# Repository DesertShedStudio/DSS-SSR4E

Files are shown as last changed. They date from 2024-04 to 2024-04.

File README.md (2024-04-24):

DSS-SSR4E
============

The "DSS-SSR4E" is a OSHWA Certified hardware design, providing four isolated SSR outputs and a single isolated
ABZ encoder input. Compatible with Mesa Ethernet Anything I/O Cards and Mesa Electronics HostMot2 configurations.

DSS-SSR4E <br>
"Desert Shed Stuido SSR x4 + Encoder"



This repository is aimed towards those who wish to manufacture their own boards. 

Media
=======

| KICAD RENDER | HAND SOLDERED PROTOTYPE  |
| --- | --- |
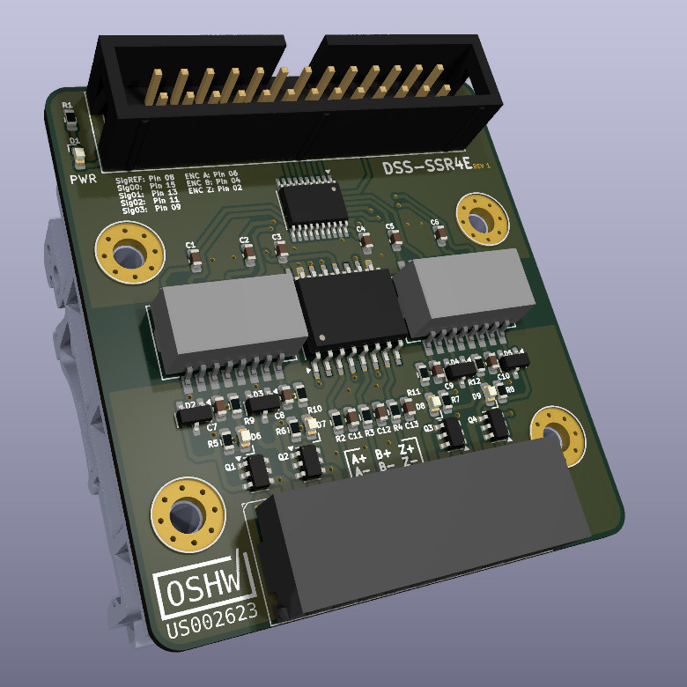
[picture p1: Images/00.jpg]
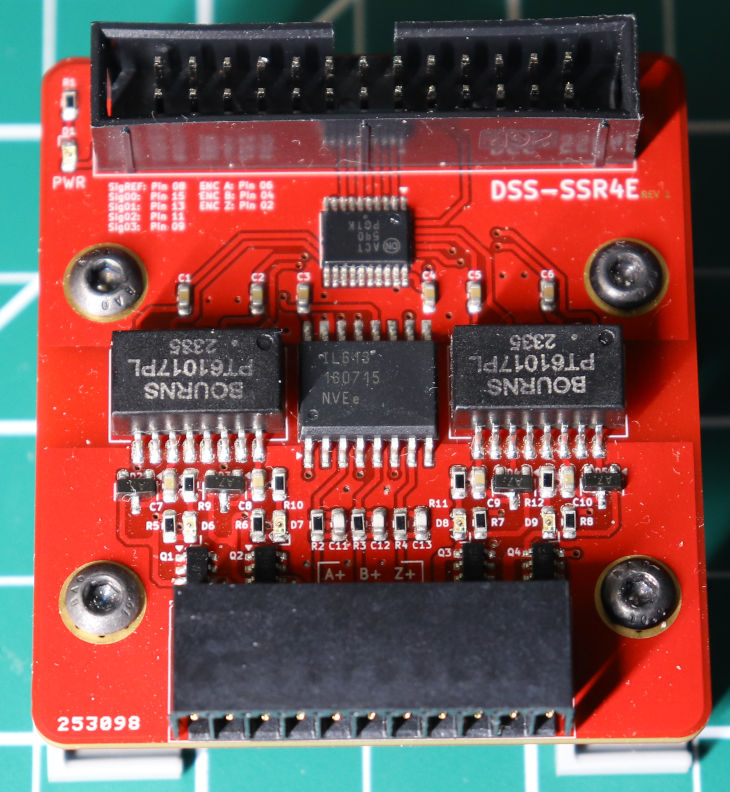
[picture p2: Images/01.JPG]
| |  |

| BENCHTEST VIDEO |
| --------------- |
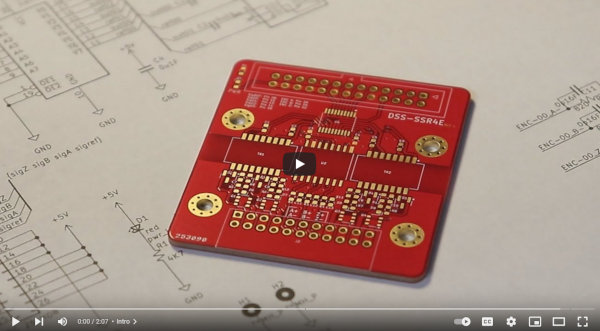
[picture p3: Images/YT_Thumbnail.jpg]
DSS-SSR4E Bench Test (https://www.youtube.com/watch?v=-4yf4lCva_A "DSS-SSR4E Bench Test")
|  |

Contribute 
===========
I am #notsponsored ! Your direct support by using my affiliate links / shopping with affiliate retailers goes a long way
in helping me to produce more open source hardware. Thank You. 

Amazon: https://amzn.to/3v1R42O <br>
Openbuilds:  https://openbuildspartstore.com/?ref=hGMJTVfeW_r4W

License
=======

DSS-SSR4E | https://github.com/DesertShedStudio/DSS-SSR4E <br>
Copyright (c) Desert Shed Studio

This source describes Open Hardware and is licensed under the CERN-OHL-S v2.

You may redistribute and modify this source and make products using it under <br>
the terms of the CERN-OHL-S v2 (https://ohwr.org/cern_ohl_s_v2.txt). <br>

This source is distributed WITHOUT ANY EXPRESS OR IMPLIED WARRANTY, <br>
INCLUDING OF MERCHANTABILITY, SATISFACTORY QUALITY AND FITNESS FOR A <br>
PARTICULAR PURPOSE. Please see the CERN-OHL-S v2 for applicable conditions.

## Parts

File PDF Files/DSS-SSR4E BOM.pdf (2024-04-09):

DSS-SSR4E

Reference | Value | Footprint | Qty
C1,C2,C3,C4,C5,C6 | 0u1F | 603 | 6
C7,C8,C9,C10 | 1000pF | 603 | 4
C11,C12,C13 | 0p16F | 603 | 3
D1 | red | 603 | 1
D2,D3,D4,D5 | BAV99 | SOT-23 | 4
D6,D7,D8,D9 | yllw | 603 | 4
H1,H2 | MH_P | Phoenix Contact 1201578 | 2
J1 | IDC 26 HDR | IDC 26 HDR 2.54 | 1
J2 | Phoenix_1844811 Phoenix Contact 1844811 | 1
Q1,Q2,Q3,Q4 | BSL606SN | TSOP-6 | 4
R1,R5,R6,R7,R8,R9,R10,R11,R12 | 4K7 | 603 | 9
R2,R3,R4 | 820 | 603 | 3
TR1,TR2 | PT61017PEL | Bourns PT61017PEL | 2
U1 | CD74ACT540 | TSSOP-20 | 1
U2 | IL613E | NVE_IL613E | 1

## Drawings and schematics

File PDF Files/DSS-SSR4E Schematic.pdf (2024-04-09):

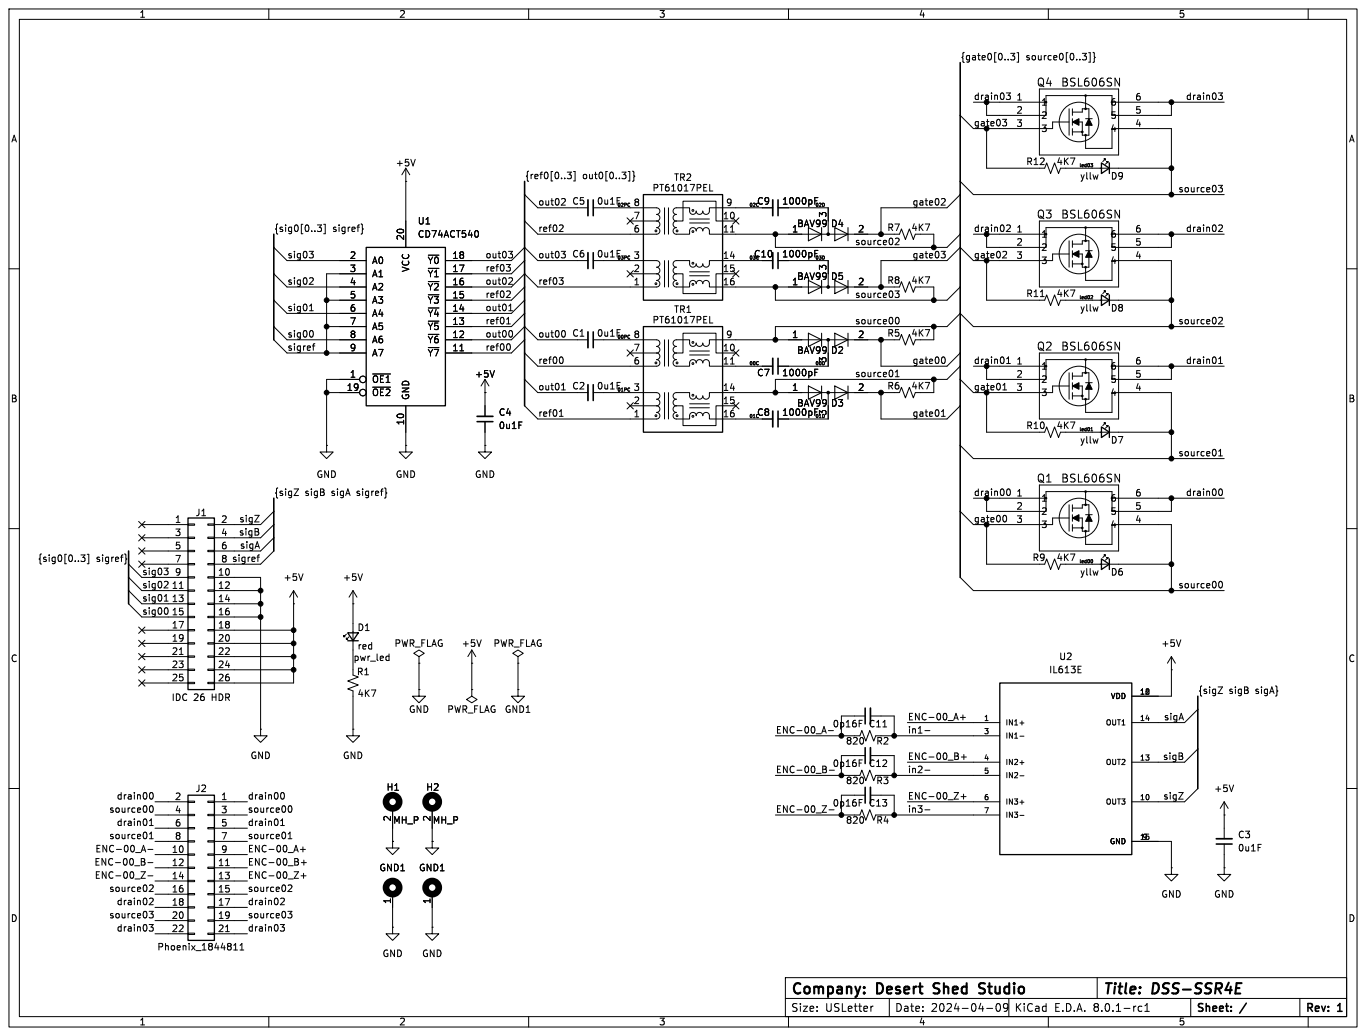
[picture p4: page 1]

{sigZ sigB sigA sigref}

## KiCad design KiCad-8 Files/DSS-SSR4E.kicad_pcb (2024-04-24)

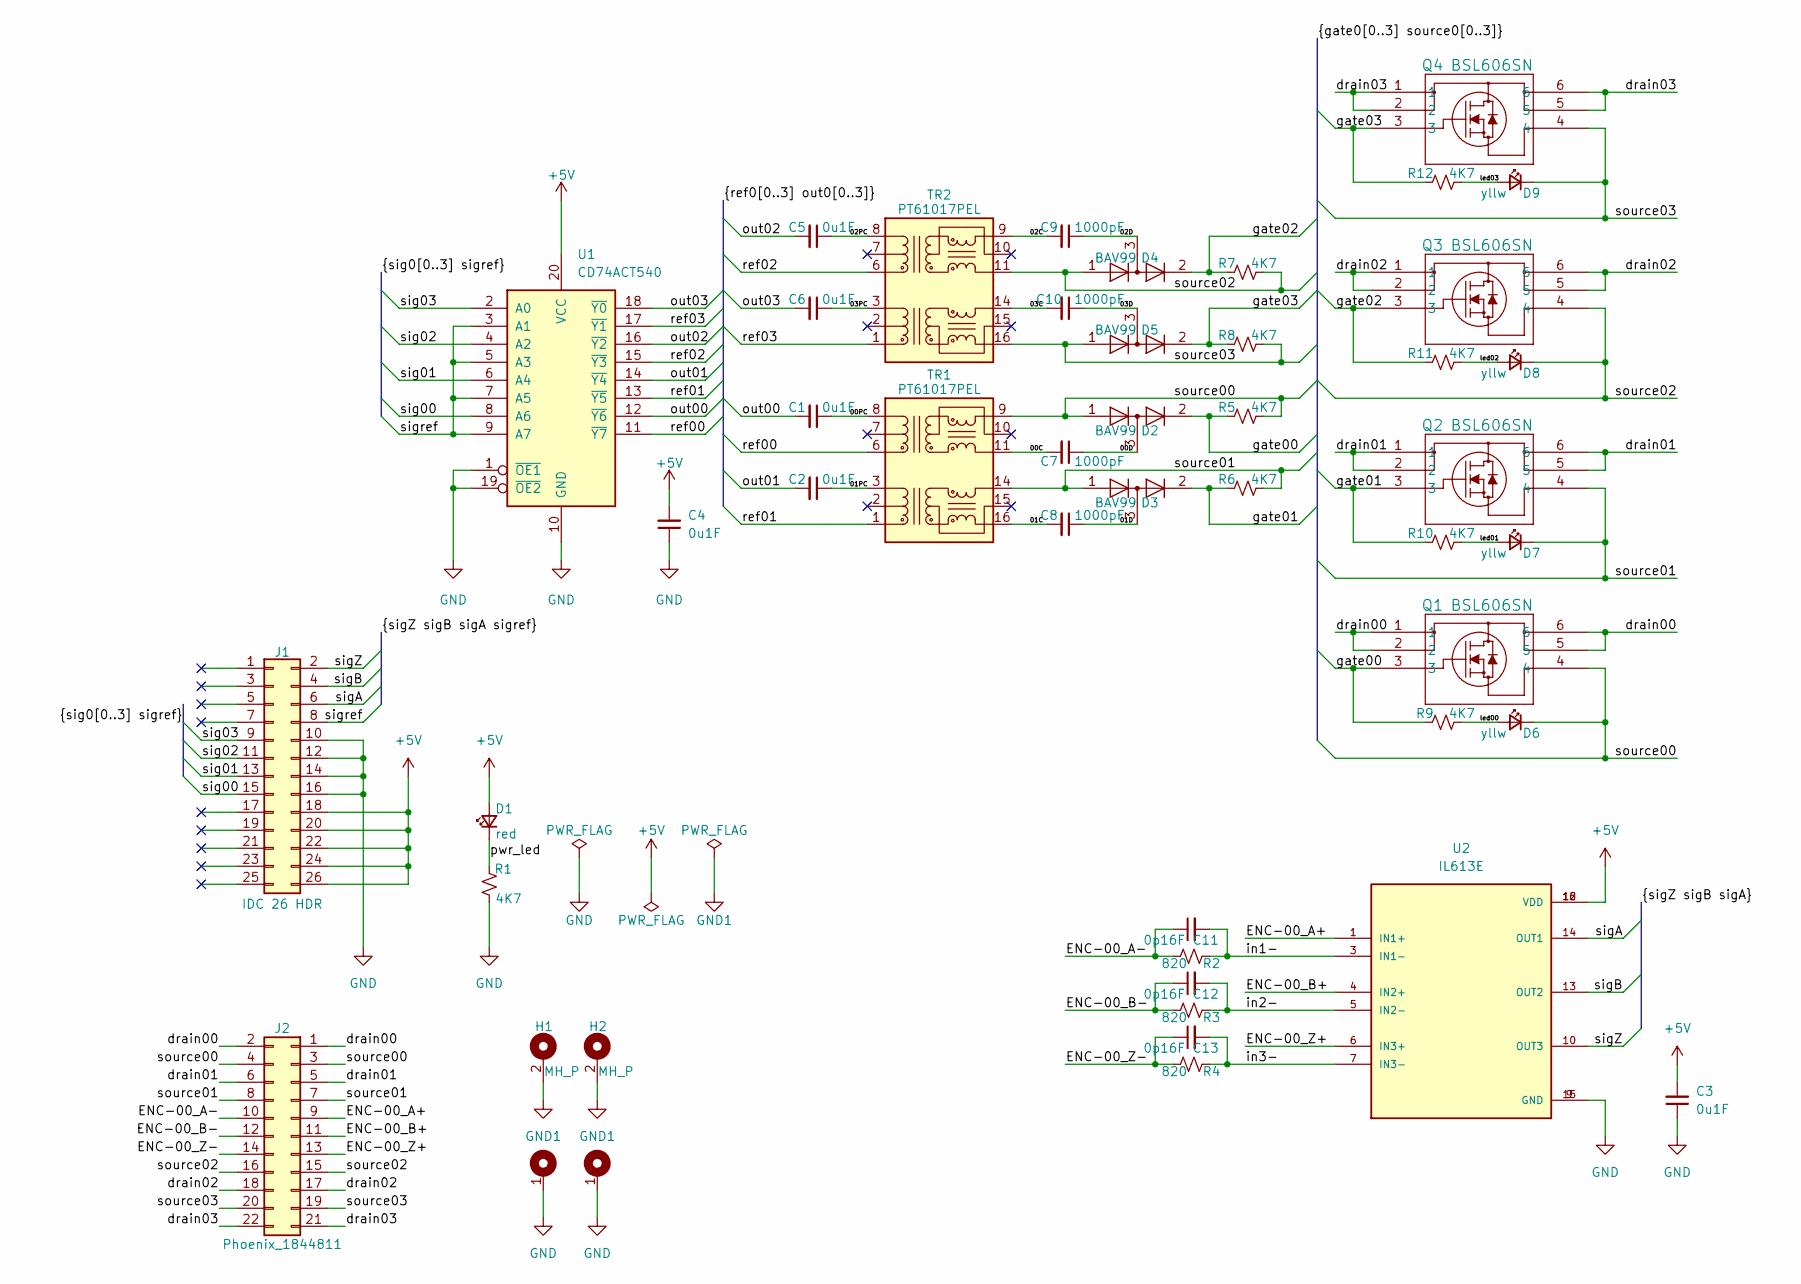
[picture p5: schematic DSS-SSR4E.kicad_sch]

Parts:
C1, C2, C3, C4, C5, C6: 0u1F; C_0603_1608Metric
C7, C8, C9, C10: 1000pF; C_0603_1608Metric
C11, C12, C13: 0p16F; C_0603_1608Metric
D1: red; LED_0603_simple_silk
D2, D3, D4, D5: BAV99; SOT-23
D6, D7, D8, D9: yllw; LED_0603_simple_silk
H1, H2: MH_P; Phoenix Contact 1201578 Pinout 1-2
J1: IDC 26 HDR; IDC 26 HDR 2.54
J2: Phoenix_1844811; Phoenix Contact 1844811
Q1, Q2, Q3, Q4: BSL606SN; TSOP-6_1.65x3.05mm_P0.95mm
R1, R5, R6, R7, R8, R9, R10, R11, R12: 4K7; R_0603_1608Metric
R2, R3, R4: 820; R_0603_1608Metric
TR1, TR2: PT61017PEL; Transformer_Ethernet_Bourns_PT61017PEL
U1: CD74ACT540; TSSOP-20_4.4x6.5mm_P0.65mm
U2: IL613E; NVE_IL613E; PARTREV AC

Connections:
+5V: C3.2, C4.2, D1.2 (A), J1.18, J1.20, J1.22, J1.24, J1.26, U1.20 (VCC), U2.12 (VDD), U2.16 (VDD)
/00C: C7.2, TR1.11 (RX+)
/00D: C7.1, D2.3 (K)
/00PC: C1.1, TR1.8 (RD-)
/01C: C8.2, TR1.16 (TX+)
/01D: C8.1, D3.3 (K)
/01PC: C2.1, TR1.3 (TD-)
/02C: C9.2, TR2.9 (RX-)
/02D: C9.1, D4.3 (K)
/02PC: C5.1, TR2.8 (RD-)
/03C: C10.2, TR2.14 (TX-)
/03D: C10.1, D5.3 (K)
/03PC: C6.1, TR2.3 (TD-)
/ENC-00_A+: J2.9, U2.1 (IN1+)
/ENC-00_A-: C11.1, J2.10, R2.2
/ENC-00_B+: J2.11, U2.4 (IN2+)
/ENC-00_B-: C12.1, J2.12, R3.2
/ENC-00_Z+: J2.13, U2.6 (IN3+)
/ENC-00_Z-: C13.1, J2.14, R4.2
/drain00: J2.1, J2.2, Q1.1, Q1.2, Q1.5, Q1.6
/drain01: J2.5, J2.6, Q2.1, Q2.2, Q2.5, Q2.6
/drain02: J2.17, J2.18, Q3.1, Q3.2, Q3.5, Q3.6
/drain03: J2.21, J2.22, Q4.1, Q4.2, Q4.5, Q4.6
/gate00: D2.2 (A), Q1.3, R5.1, R9.1
/gate01: D3.2 (A), Q2.3, R6.1, R10.1
/gate02: D4.2 (A), Q3.3, R7.1, R11.1
/gate03: D5.2 (A), Q4.3, R8.1, R12.1
/in1-: C11.2, R2.1, U2.3 (IN1-)
/in2-: C12.2, R3.1, U2.5 (IN2-)
/in3-: C13.2, R4.1, U2.7 (IN3-)
/led00: D6.2 (A), R9.2
/led01: D7.2 (A), R10.2
/led02: D8.2 (A), R11.2
/led03: D9.2 (A), R12.2
/out00: C1.2, U1.12 (~Y6)
/out01: C2.2, U1.14 (~Y4)
/out02: C5.2, U1.16 (~Y2)
/out03: C6.2, U1.18 (~Y0)
/pwr_led: D1.1 (K), R1.1
/ref00: TR1.6 (RD+), U1.11 (~Y7)
/ref01: TR1.1 (TD+), U1.13 (~Y5)
/ref02: TR2.6 (RD+), U1.15 (~Y3)
/ref03: TR2.1 (TD+), U1.17 (~Y1)
/sig00: J1.15, U1.8 (A6)
/sig01: J1.13, U1.6 (A4)
/sig02: J1.11, U1.4 (A2)
/sig03: J1.9, U1.2 (A0)
/sigA: J1.6, U2.14 (OUT1)
/sigB: J1.4, U2.13 (OUT2)
/sigZ: J1.2, U2.10 (OUT3)
/sigref: J1.8, U1.3 (A1), U1.5 (A3), U1.7 (A5), U1.9 (A7)
/source00: D2.1 (K), D6.1 (K), J2.3, J2.4, Q1.4, R5.2, TR1.9 (RX-)
/source01: D3.1 (K), D7.1 (K), J2.7, J2.8, Q2.4, R6.2, TR1.14 (TX-)
/source02: D4.1 (K), D8.1 (K), J2.15, J2.16, Q3.4, R7.2, TR2.11 (RX+)
/source03: D5.1 (K), D9.1 (K), J2.19, J2.20, Q4.4, R8.2, TR2.16 (TX+)
GND: C3.1, C4.1, H1.1, H2.1, J1.10, J1.12, J1.14, J1.16, R1.2, U1.1 (~OE1), U1.10 (GND), U1.19 (~OE2), U2.9 (GND), U2.15 (GND)
GND1: H1.2, H2.2

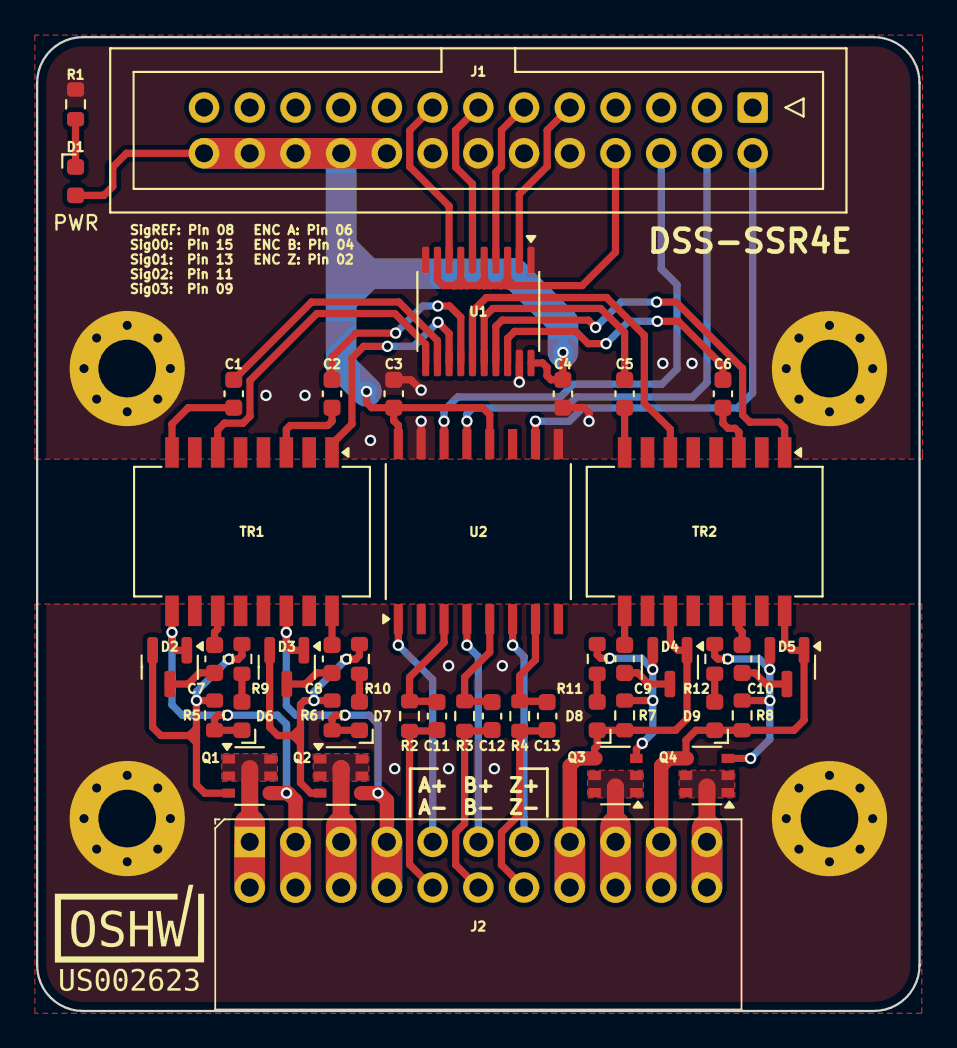
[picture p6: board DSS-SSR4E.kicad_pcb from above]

Board: 2 copper layers, 49.0 x 54.1 mm, 46 parts (0 on the bottom side), 57 nets.

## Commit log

2024-04-09 Add files via upload
    Initial file upload.
    [DSS-SSR4E-B_Cu.gbr, DSS-SSR4E-B_Mask.gbr, DSS-SSR4E-B_Paste.gbr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]
2024-04-24 update gerber files for OSHWA cert.
    [DSS-SSR4E-B_Cu.gbr, DSS-SSR4E-B_Mask.gbr, DSS-SSR4E-B_Paste.gbr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]
2024-04-24 update kicad render for OSHWA cert.
2024-04-24 update kicad files for OSHWA cert.
    [DSS-SSR4E.kicad_pcb, DSS-SSR4E.kicad_sch]
